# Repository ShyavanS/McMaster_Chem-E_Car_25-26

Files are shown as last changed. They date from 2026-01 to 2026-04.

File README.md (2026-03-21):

# McMaster_Chem-E_Car_25-26
The codebase for the McMaster Chem-E Car Team from 2025-2026.

This project uses an Adafruit Feather RP2040 Adalogger microcontroller programmed in the Arduino programming language. The car runs off a chemical reaction and is stopped by a chemical reaction as well. However, the code and the microcontroller are used to start the stopping reaction and stir the mixtures while monitoring it to identify when to stop based on a temperature threshold. It also uses an IMU to keep the car going straight, a servo for starting the stopping reaction, a switching circuit composed of solid-state relays to run the drive motors, and a motor driver for two auxiliary motors for stirring the braking reaction and operating accessories. The car's main drive system will be powered from a hydrogen fuel cell while the remaining auxiliary systems are powered from a smaller Li-Po battery.

The major components used are as follows:<br />
1 - N20 100 RPM Motor (for drive system)<br />
1 - N20 1000 RPM Motor (for reaction stirring mechanism)<br />
1 - N20 30 RPM Motor (for door actuation mechanism)<br />
3 - SER0039 Servo Motor (for initially mixing reactants & steering)<br />
1 - DRV8847 Motor Driver (for auxiliary motors)<br />
1 - AMT103 Rotary Encoder (for datalogging to tune braking model only)<br />
1 - CS326 Solid State Relay (for drive motors)<br />
1 - AD623 Instrumentation Amplifier (for braking reaction sensing setup)<br />
1 - GL5516 Phootoresistor (for braking reaction sensing setup)<br />
1 - 5 mm White LED (for braking reaction sensing setup)<br />
1 - REF2033 Dual-Output Voltage Reference (for braking reaction sensing setup)<br />
1 - INA219 Bidirectional Current/Power Monitor (for propulsion reaction datalogging & safety)<br />
1 - WS2812B LED Strip (for auxiliary lighting)<br />
1 - 2.5W Speaker (for auxiliary use)<br />
1 - PAM8302A Class D Amplifier (for driving speaker)<br />
1 - Toggle Switch (for enable line)<br />
1 - Adafruit 9-DOF Orientation IMU Fusion Breakout (BNO085 for logging/maintaining heading)<br /> 
1 - Adafruit Feather RP2040 Adalogger Microcontroller (for controlling the car)<br />
1 - 30W Hydrogen Fuel Cell  (for drive power)<br />
1 - 5000 mAh Li-Po Battery (for auxiliary power)<br />

This repository also contains the custom-made PCB design for the component wiring we are using this year. The design was made using Altium, source files & gerber files are present in this repository.

The main objective of the competition is to design a small car to carry a certain amount of weight a set distance while powering and stopping the vehicle with a chemical reaction. The distance and weight vary each year. The compectition is hosted by the American Institute of Chemical Engineers (AIChE).

Makes use of [pimoroni's encoder-pio driver](https://github.com/pimoroni/pimoroni-pico/tree/encoder-pio/drivers/encoder-pio) to count encoder ticks on the PIOs of the RP2040 to prefvent lost ticks due to higher priority interrupts and increase accuracy while decreasing CPU load. Minor modifications were made to remove debouncing functionality & delays.

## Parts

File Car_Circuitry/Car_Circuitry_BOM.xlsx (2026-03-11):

Comment | Description | Designator | Footprint | LibRef | Quantity
REF2033QDDCRQ1 | Integrated Circuit | AREF | SOT95P280X110-5N | REF2033QDDCRQ1 | 1
B2B-XH-A(LF)(SN) | CONN HEADER VERT 2POS 2.5MM | AUXM, DRVM, LEDB, PROP, SPKR, STRM, SW, TRB | FP-B2B-XH-A_LF_SN-MFG | CMP-2000-05888-3 | 8
TPS61023DRLT | Integrated Circuit | BOOST | SOTFL50P160X60-6N | TPS61023DRLT | 1
100 nF | Capacitor | C1, C4, C5, C8, C9, C13 | CAPC2012X95N | CL21B104KBCNNNC | 6
10 μF | Capacitor | C2, C6, C14 | CAPC2012X140N | CL21B106KOQNNNE | 3
1 μF | Capacitor | C3 | C0402C104J4RACTU | C0402C105K9PACTU | 1
10 μF | Capacitor Polarised | C7 | CAPPM3528X210N | 293D106X9016B2TE3 | 1
100 μF | Capacitor | C10 | GRM31x | GRM31CD80J107MEA8K | 1
220 pF | Capacitor | C11, C12 | GRM033D70J224ME01D | GRM033R71C221KA01D | 2
22 μF | Capacitor | C15, C16 | CAPC3216X180N | CL31B226KPHNNNE | 2
SMBJ18CA | TVS Diode (Bi-directional) | D1 | DIOM5436X261N | SMBJ18CA | 1
PAM8302AASCR | Integrated Circuit | DAMP | SOP65P490X110-8N | PAM8302AASCR | 1
DRV8847PWPR | Integrated Circuit | DRV | SOP65P640X120-17N | DRV8847PWPR | 1
61300411821 | THT Vertical Socket Header WR-PHD, Pitch 2.54 mm, Single Row, 4 pins | ENC | 61300411821 | CMP-1502-01316-4 | 1
MPZ1608S221ATA00 | Power line Ferrite Bead 220Ω @ 100MHz 2.2A DCR 0.05Ω SMD 0603 | FB1, FB2 | FP-MPZ1608-0_8-MFG | CMP-08257-000028-1 | 2
AD623ARZ-R7 | Integrated Circuit | IAMP | SOIC127P600X175-8N | AD623AR-REEL7 | 1
1 μH | Inductor | L1 | 74438357010 | 74438357010 | 1
B3B-XH-A(LF)(SN) | CONN HEADER VERT 3POS 2.5MM | LEDA, SVOB, SVOP, SVOS | FP-B3B-XH-A_LF_SN-MFG | CMP-17439-000014-3 | 4
Feather RP2040 Adalogger | Adafruit Microcontroller | MCU | 2796 | 2796 | 1
100 mΩ | Resistor | R1 | RESC2013X65N | RCWE0805R100FKEA | 1
400 Ω | Resistor | R2, R3 | RESC1608X46N | PAT0603E4000BST1 | 2
680 mΩ | Resistor | R4, R5 | ERJ6_B_BW_R_LW_CW_D | ERJ-6DQJR68V | 2
10 kΩ | Resistor | R6, R7 | RESC1005X40N | RC0402JR-0710KL | 2
200 kΩ | Resistor | R8 | ERA6AEB101V | ERA-6AEB204V | 1
330 Ω | Resistor | R9 | RESC1005X40N | RC0402FR-07330RL | 1
5 kΩ | Resistor | R10, R11, R13 | RESC0603X26N | TNPW02015K00BEED | 3
150 Ω | Resistor | R12 | RESC2012X60N | RK73B2ATTD151J | 1
100 kΩ | Resistor | R14 | ERJ8ENF1000V | ERJ-8ENF1003V | 1
732 kΩ | Resistor | R15 | ERJ8ENF1000V | ERJ-8ENF7323V | 1
CS326 | Relay or Contactor | SSR | SOP254P1030X390-8N | CS326 | 1
INA219BIDR | Integrated Circuit | VAM | SOIC127P600X175-8N | INA219BIDR | 1

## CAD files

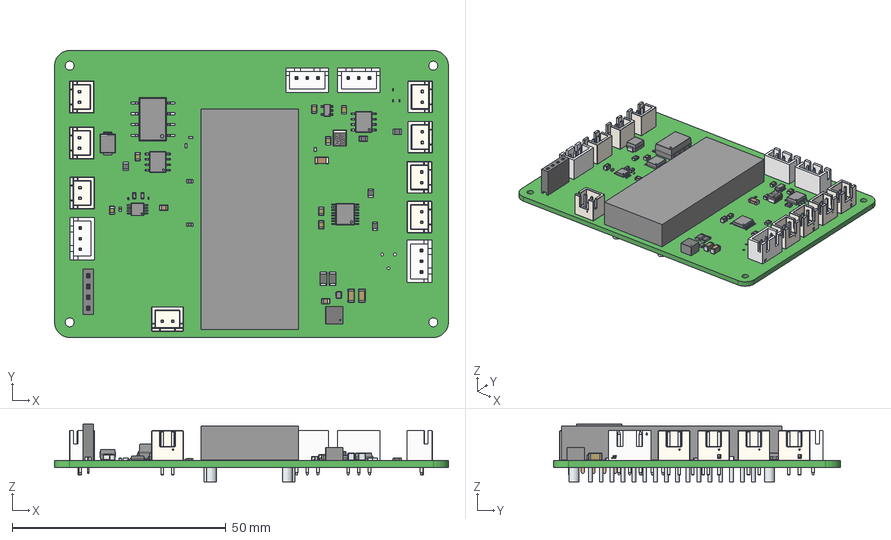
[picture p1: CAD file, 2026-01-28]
Car_Circuitry/Car_Circuitry.step
92.1 x 67.1 x 13.5 mm
PinsArrayLR x 5
term1 x 4
term2 x 4
B2B-XH-A x 8
JST Logo adjustable x 8
solidBody x 5
solidTop x 5
solidTerminal1
solidTerminal2
solidTerminal3
GCM31A5C2J820JX01J_3
GCM31A5C2J820JX01J_2
GCM31A5C2J820JX01J
PinsArrayL
PinsArrayR
terminals x 2
logo x 2
Pins x 4
Marking x 4
JST Logo x 4
6130xx11821_PIN x 4
body_SSMC_4030
land_pattern_SSMC_4020 x 2
Terminal x 4
Leads x 32
ThermalPad
BODY-SOT
PIN1-ID

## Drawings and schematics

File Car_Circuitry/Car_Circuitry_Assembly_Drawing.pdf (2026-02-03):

13

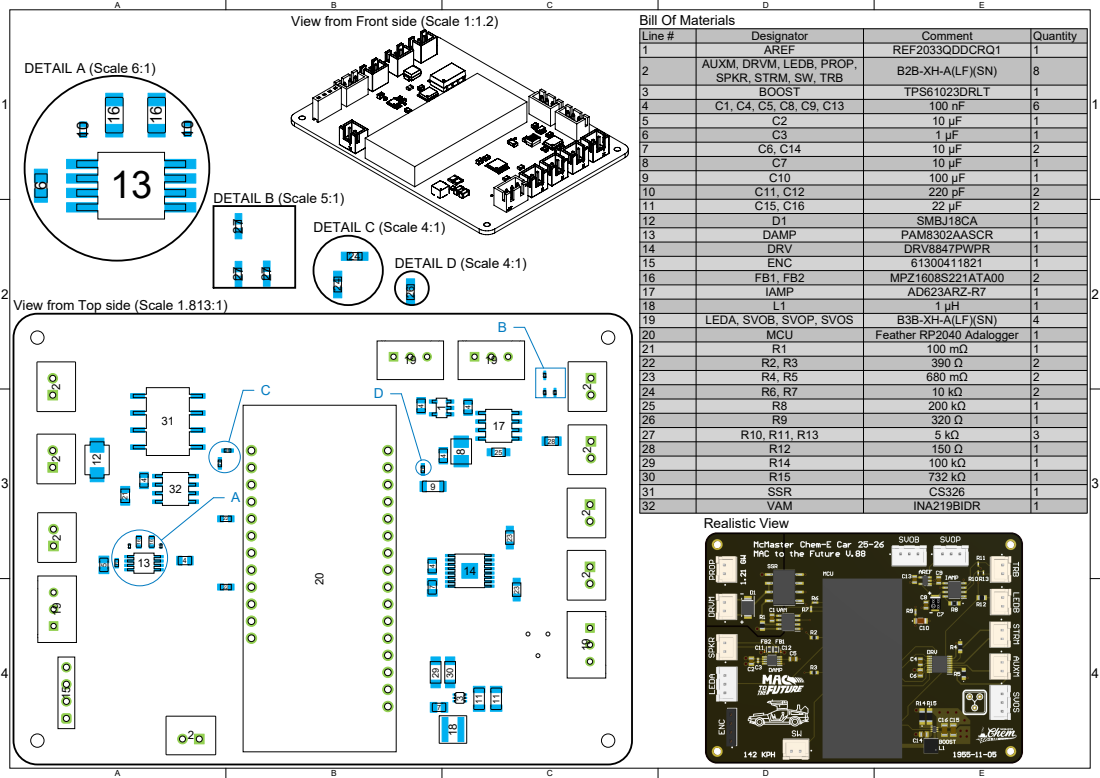
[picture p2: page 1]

View from Front side (Scale 1:1.2)

Line # | Designator | Comment | Quantity
1 | AREF | REF2033QDDCRQ1 | 1
2 | AUXM, DRVM, LEDB, PROP, SPKR, STRM, SW, TRB | B2B-XH-A(LF)(SN) | 8

3 | BOOST | TPS61023DRLT | 1
4 | C1, C4, C5, C8, C9, C13 | 100 nF | 6
5 | C2 | 10 μF | 1
6 | C3 | 1 μF | 1
7 | C6, C14 | 10 μF | 2
8 | C7 | 10 μF | 1
9 | C10 | 100 μF | 1
10 | C11, C12 | 220 pF | 2
11 | C15, C16 | 22 μF | 2
12 | D1 | SMBJ18CA | 1
13 | DAMP | PAM8302AASCR | 1
14 | DRV | DRV8847PWPR | 1
15 | ENC | 61300411821 | 1
16 | FB1, FB2 | MPZ1608S221ATA00 | 2
17 | IAMP | AD623ARZ-R7 | 1
18 | L1 | 1 μH | 1
19 | LEDA, SVOB, SVOP, SVOS | B3B-XH-A(LF)(SN) | 4
20 | MCU | Feather RP2040 Adalogger | 1
21 | R1 | 100 mΩ | 1
22 | R2, R3 | 390 Ω | 2
23 | R4, R5 | 680 mΩ | 2
24 | R6, R7 | 10 kΩ | 2
25 | R8 | 200 kΩ | 1
26 | R9 | 320 Ω | 1
27 | R10, R11, R13 | 5 kΩ | 3
28 | R12 | 150 Ω | 1

View from Top side (Scale 1.813:1)

29 | R14 | 100 kΩ | 1
30 | R15 | 732 kΩ | 1
31 | SSR | CS326 | 1
32 | VAM | INA219BIDR | 1

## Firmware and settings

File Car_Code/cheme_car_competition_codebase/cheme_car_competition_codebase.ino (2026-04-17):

// McMaster Chem-E Car Team
// Chem-E Car Competition Code - 25/26

/*
The code to be used at the Chem-E Car competition to run the car. Makes use of
an RP2040 microcontroller to drive the car and stop at a specified distance.
More information is available in the readme.
*/

// Included libraries
#include <Adafruit_BNO08x.h>
#include <Servo.h>
#include <Adafruit_NeoPixel.h>
#include <Wire.h>
#include <BackgroundAudio.h>
#include <PWMAudio.h>
#include <SdFat.h>
#include "hardware/timer.h"
#include "pico/stdlib.h"

#define NUM_LEDS 1    // Status LED
#define STRIP_LEDS 22 // LED Strip

// Define drive and brake SSR pins
#define DRIVE_PIN 9
#define BRAKE_PIN 13

// Define the PWM pins for the stir bar motors
#define BRAK_STIR_PWM_1 A3
#define BRAK_STIR_PWM_2 24

// Define servo pins
#define BRAK_SERVO_PWM 11
#define PROP_SERVO_PWM 4
#define STEERING_SERVO_PWM 25

// Define Auxillary DC Motor Pins
#define AUXDC_PWM_1 6
#define AUXDC_PWM_2 5

#define STRIP_PIN 10 // Light pin

#define TURBIDITY_SENS A2 // Pin for the turbidity sensor data line(right encoder and braking sensor switched pins)
#define BNO08X_RESET -1   // No reset pin for IMU over I2C, only enabled for SPI
#define SD_CS_PIN 23      // Define chip select pin for SD card
#define A219_I2C 0x40     // I2C address for current/voltage sensor
#define AUDIO_OUT 12      // Define audio output pin

// Struct for Euler Angles
struct euler_t
{
  float yaw;
  float pitch;
  float roll;
} ypr;

// Enumeration for door commands
enum door_cmd
{
  DOOR_STOP,
  DOOR_OPEN,
  DOOR_CLOSE
};

// Enumeration for multicore commands
enum mutlicore_cmd
{
  PLAY_DOOR_OPEN = 1,
  PLAY_DOOR_CLOSE,
  PLAY_TIME_TRAVEL,
  PLAY_TIME_CIRCUIT,
  STATUS_ERROR,
  STATUS_STARTED,
  STATUS_STOPPED,
  SD_INITIALIZED
};

// Create servo objects
Servo brak_servo;
Servo prop_servo;
Servo steering_servo;

// Create BNO085 instance
Adafruit_BNO08x bno08x(BNO08X_RESET);
sh2_SensorValue_t sensor_value;

Adafruit_NeoPixel pixel(NUM_LEDS, PIN_NEOPIXEL, NEO_GRB + NEO_KHZ800); // Status LED
Adafruit_NeoPixel strip(STRIP_LEDS, STRIP_PIN, NEO_GRB + NEO_KHZ800);  // Strip LEDs

// Define files
SdFat sd;
FsFile audio_file;
String door_close_sound = "door_close_sound.mp3";
String time_circuit_sound = "time_circuit_sound.mp3";
String time_travel_sound = "time_travel_sound.mp3";
String door_open_sound = "door_open_sound.mp3";
String theme_music = "theme_music.mp3";
SdSpiConfig config(SD_CS_PIN, DEDICATED_SPI, SD_SCK_MHZ(16), &SPI1);
String file_name;

// Set up audio output using PWM
PWMAudio pwm(AUDIO_OUT);
BackgroundAudioMP3 mp3(pwm); // create the mp3 player object and decoder
uint8_t filebuff[512];       // allocates 512 bytes of memory to temporarily store audio data before processing

// LED variables
bool breath_status = false;
bool fluxing = false;
bool time_jump = false;
int breath_brightness = 0;
int t = 0;
uint32_t tic;
uint32_t toc;

bool sd_init = false; // SD intialization flag

// Runtime flags
volatile bool running = true;
volatile bool audio_trig = false;
volatile unsigned int audio_played = 0;

// The target yaw angle to keep car straight
const float GOAL_YAW = 0.0;

// Rejection threshold for noise in IMU measurements
const float REJECT_THRESHOLD = 3.0;

// define turbidity threshold for braking
const float TURB_THRESHOLD = 3500.0;

// Define voltage & current monitor variables
uint16_t raw_bus;
int16_t raw_current;
double bus_voltage;
double current_mA;

// Define IMU variables
double raw_yaw;        // raw yaw angle
double prev_yaw;       // previous unwrapped yaw angle
double yaw;            // unwrapped yaw angle
double init_yaw = 0.0; // initial yaw angle
double yaw_diff = 0.0; // yaw angle difference

double turbidity; // turbidity counts

// Keeping track of time
double curr_time = 0.0f;
double prev_time = 0.0f;
uint32_t start_time;

// PID loop variables
double error = 0.0;      // Proportional error
double last_error = 0.0; // Derivative error
double sum_error = 0.0;  // Integral error

// Current values obtained through Ziegler–Nichols method with K_u = 30 & T_u = 266.7 ms.
// Divide derivative term by 100 to make sense on this timescale
// Added 4 to proportional since speed was changed with higher gearing
const float K_P = 22.0;  // Proportional weighting
const float K_I = 0.135; // Integral weighting
const float K_D = 0.612; // Derivative weighting

// Offsets & constants for PID
const int SERVO_ANGLE = 1475;
const int MAX_OFFSET = 1024;
const int YAW_REF = 90;

/*
Description: Subroutine to close both drive and brake SSR.
Inputs:      void
Outputs:     void
Parameters:  void
Returns:     void
*/
void reset_ssr()
{
  digitalWrite(DRIVE_PIN, LOW);
  digitalWrite(BRAKE_PIN, LOW);
}

/*
Description: Subroutine to drive car forward.
Inputs:      void
Outputs:     void
Parameters:  void
Returns:     void
*/
void drive_ssr()
{
  reset_ssr();
  busy_wait_ms(1);
  digitalWrite(DRIVE_PIN, HIGH);
}

/*
Description: Subroutine to stop car and brake motors.
Inputs:      void
Outputs:     void
Parameters:  void
Returns:     void
*/
void brake_ssr()
{
  reset_ssr();
  busy_wait_ms(1);
  digitalWrite(BRAKE_PIN, HIGH);
}

/*
Description: Subroutine to dump reactants into vessel.
Inputs:      void
Outputs:     void
Parameters:  (Servo)servo, (int)angle_us, (int)delay_ms
Returns:     void
*/
void servo_dump(Servo servo, int angle_us, int delay_ms)
{
  // Rotate to specified position
  servo.writeMicroseconds(angle_us);
  busy_wait_ms(500);
  servo.writeMicroseconds(angle_us);

  busy_wait_ms(delay_ms); // Wait specified delay

  // Return to default position
  servo.writeMicroseconds(450);
  busy_wait_ms(500);
  servo.writeMicroseconds(450);
}

/*
Description: Subroutine to set speed for reaction stir motors.
Inputs:      void
Outputs:     void
Parameters:  (int)stir_pin_1, (int)stir_pin_2, (int)speed
Returns:     void
*/
void start_stir(int stir_pin_1, int stir_pin_2, int speed)
{
  digitalWrite(stir_pin_1, LOW); // For fast decay
  analogWrite(stir_pin_2, 255);  // Set motor to max for a kickstart
  busy_wait_ms(1000);
  digitalWrite(stir_pin_1, LOW);  // For fast decay
  analogWrite(stir_pin_2, speed); // Set motor to speed obtained through testing
}

/*
Description: Subroutine to stop reaction stir motors.
Inputs:      void
Outputs:     void
Parameters:  (int)stir_pin_1, (int)stir_pin_2
Returns:     void
*/
void stop_stir(int stir_pin_1, int stir_pin_2)
{
  digitalWrite(stir_pin_1, LOW); // For fast decay
  digitalWrite(stir_pin_2, LOW); // Stop motor
}

/*
Description: Subroutine to command the door motor
Inputs:      void
Outputs:     void
Parameters:  (door_cmd)cmd, (int)speed
Returns:     void
*/
void door_motor(door_cmd cmd, int speed)
{
  switch (cmd)
  {
  case DOOR_STOP:
    analogWrite(AUXDC_PWM_1, 0);
    analogWrite(AUXDC_PWM_2, 0);
    break;
  case DOOR_OPEN:
    analogWrite(AUXDC_PWM_1, 0);
    analogWrite(AUXDC_PWM_2, speed);
    break;
  case DOOR_CLOSE:
    analogWrite(AUXDC_PWM_1, speed);
    analogWrite(AUXDC_PWM_2, 0);
    break;
  default:
    break;
  }
}

/*
Description: Subroutine to set the desired reports on the IMU.
Inputs:      void
Outputs:     void
Parameters:  void
Returns:     void
*/
void set_reports(void)
{
  if (!bno08x.enableReport(SH2_ROTATION_VECTOR))
  {
    exit(0);
  }
}

/*
Description: Subroutine convert quaternions from the IMU into euler angles to obtain yaw.
Inputs:      void
Outputs:     void
Parameters:  (float)qr, (float)qi, (float)qj, (float)qk, (euler_t)*ypr, (bool)degrees
Returns:     void
*/
void quaternion_to_euler(float qr, float qi, float qj, float qk, euler_t *ypr, bool degrees = false)
{
  float sqr = sq(qr);
  float sqi = sq(qi);
  float sqj = sq(qj);
  float sqk = sq(qk);

  ypr->yaw = atan2(2.0 * (qi * qj + qk * qr), (sqi - sqj - sqk + sqr));
  ypr->pitch = asin(-2.0 * (qi * qk - qj * qr) / (sqi + sqj + sqk + sqr));
  ypr->roll = atan2(2.0 * (qj * qk + qi * qr), (-sqi - sqj + sqk + sqr));

  if (degrees)
  {
    ypr->yaw *= RAD_TO_DEG;
    ypr->pitch *= RAD_TO_DEG;
    ypr->roll *= RAD_TO_DEG;
  }
}

/*
Description: Pointer subroutine for euler angles.
Inputs:      void
Outputs:     void
Parameters:  (sh2_RotationVectorWAcc_t)*rotational_vector, (float)qi, (euler_t)*ypr, (bool)degrees
Returns:     void
*/
void quaternion_to_euler_RV(sh2_RotationVectorWAcc_t *rotational_vector, euler_t *ypr, bool degrees = false)
{
  quaternion_to_euler(rotational_vector->real, rotational_vector->i, rotational_vector->j, rotational_vector->k, ypr, degrees);
}

/*
Description: PID loop subroutine to adjust steering angle.
Inputs:      (double)error, (double)sum_error, (double)last_error, (double)curr_time, (double)prev_time
Outputs:     (int)adj_pid_output
Parameters:  void
Returns:     void
*/
void pid_loop(void)
{
  // Generate output of controller based on constants & errors
  double pid_output = (error * K_P + sum_error * K_I + (error - last_error) / (curr_time - prev_time) * K_D) / YAW_REF * MAX_OFFSET;
  int adj_pid_output = max(min(round(pid_output), MAX_OFFSET), -MAX_OFFSET); // Clamp output to bounds

  // Get IMU reading to update error values
  bno08x.getSensorEvent(&sensor_value);
  quaternion_to_euler_RV(&sensor_value.un.rotationVector, &ypr, true);

  // Process yaw angle
  raw_yaw = ypr.yaw;
  unwrap_yaw();
  yaw_diff = yaw - init_yaw;

  // Update errors
  last_error = error;
  error = GOAL_YAW - yaw_diff;
  sum_error = max(min(sum_error + error, MAX_OFFSET), -MAX_OFFSET);

  // Write to servos
  steering_servo.writeMicroseconds(SERVO_ANGLE + adj_pid_output);
}

/*
Description: Subroutine to fetch turbidity samples and output the average value.
Inputs:      void
Outputs:     void
Parameters:  (int)samples
Returns:     (float)turbidity
*/
float fetch_turb(int samples)
{
  // calculate turbidity (avg of # measurements)
  float turbidity = 0.0f;

  for (int i = 0; i < samples; i++)
  {
    turbidity += (double)analogRead(TURBIDITY_SENS);
  }
  turbidity = turbidity / (double)samples;

  return turbidity;
}

/*
Description: Subroutine to unwrap yaw angle to prevent discontinuities in the function over time.
Inputs:      (double)raw_yaw, (double)prev_yaw
Outputs:     (double)yaw
Parameters:  void
Returns:     void
*/
void unwrap_yaw(void)
{
  double delta = raw_yaw - prev_yaw;

  delta = fmod(delta + 180.0, 360.0);

  if (delta < 0.0)
  {
    delta += 360.0;
  }

  delta -= 180.0;

  // Reject any sudden noisy spikes
  if (fabs(delta) > REJECT_THRESHOLD)
  {
    yaw = prev_yaw;
    prev_yaw = yaw;
  }
  else
  {
    yaw = prev_yaw + delta;
    prev_yaw = yaw;
  }
}

/*
Description: Turn on speaker before playing audio
Inputs:      void
Outputs:     void
Parameters:  void
Returns:     void
*/
void stop_speaker(void)
{
  while (!audio_file && !mp3.done())
    ;

  memset(filebuff, 0, 512);
  mp3.write(filebuff, 512);
}
/*
Description: Send audio data chunks to the decoder and close file when done
Inputs:      void
Outputs:     void
Parameters:  void
Returns:     void
*/
void send_audio(void)
{
  // If an audio file is open and the decoder buffer has enough space for more audio data
  if (audio_file && mp3.availableForWrite() > 512)
  {
    // read 512 bytes from the audio file and send to the decoder
    int len = audio_file.read(filebuff, 512);
    mp3.write(filebuff, len);

    // if the audio data was shorter than 512 bytes, we've reached the end of the file
    if (len != 512)
    {
      audio_trig = false;
      audio_played++;

      audio_file.close();
      stop_speaker();
    }
  }
}

/*
Description: Activates Orange/Blue car lights
Inputs: void
Outputs: void
Parameters: void
Returns: void
*/
void car_lights(void)
{
  if (!breath_status)
  {
    breath_brightness += 10;

    if (breath_brightness >= 255)
    {
      breath_brightness = 255;
      breath_status = true;
    }

    for (int i = 1; i < STRIP_LEDS; i++)
    {
      strip.setPixelColor(i, 0, (int)255 * breath_brightness / 255, (int)255 * breath_brightness / 255); // set rest of pixels blue for now...
    }
  }
  else
  {
    int spark = random(0, 50);

    if (spark < 5)
    {
      for (int i = 1; i < STRIP_LEDS; i++)
      {
        strip.setPixelColor(i, 255, 40, 0); // set rest of pixels orange for now...
      }
    }
    else
    {
      for (int i = 1; i < STRIP_LEDS; i++)
      {
        strip.setPixelColor(i, 0, 255, 255); // set rest of pixels blue for now...
      }
    }
  }

  strip.setPixelColor(0, 255, 255, 255);
  strip.show();
}

/*
Description: Turns on flux capacitor light
Inputs: void
Outputs: void
Parameters: void
Returns: void
*/
void flux_cap(void)
{
  t++;

  // Base sinusoid + flicker
  float wave = (sin(t * 0.1) + 1) * 0.5;
  int base = 120 + wave * 100;
  int flicker = random(-40, 40);
  int b = constrain(base + flicker, 0, 255);

  // Sudden burst for extra random behaviour
  int burst = random(0, 50);

  if (burst < 10)
  {
    b = 255;
  }
  else if (burst > 40)
  {
    b = 0;
  }

  strip.setPixelColor(0, b, b, b);
  strip.show();
}

/*
Description: Helper function to write value to register over I2C
Inputs: void
Outputs: void
Parameters: (uint8_t)address, (uint8_t)reg, (uint16_t)value
Returns: void
*/
void write_register(uint8_t address, uint8_t reg, uint16_t value)
{
  Wire.beginTransmission(address);

  Wire.write(reg);
  Wire.write((value >> 8) & 0xFF); // MSB
  Wire.write(value & 0xFF);        // LSB

  Wire.endTransmission();
}

/*
Description: Helper function to read value from register over I2C
Inputs: void
Outputs: void
Parameters: (uint8_t)address, (uint8_t)reg
Returns: (uint16_t)value
*/
uint16_t read_register(uint8_t address, uint8_t reg)
{
  Wire.beginTransmission(address);
  Wire.write(reg);
  Wire.endTransmission();

  Wire.requestFrom(address, (uint8_t)2); // Request 2 bytes

  // If data available then return it
  if (Wire.available() >= 2)
  {
    uint16_t value = Wire.read() << 8;
    value |= Wire.read();
    return value;
  }

  return 0; // Otherwise return 0
}

/*
Description: Arduino core 0 setup subroutine.
Inputs:      void
Outputs:     void
Parameters:  void
Returns:     void
*/
void setup(void)
{
  // Intitalize Voltage/Current Sensor
  Wire.begin();

  // Write to config register (0x00), Sets it to 16V bus range, Gain /4, 12 bit ADC, Continuous Mode, 8-sample averaging
  write_register(A219_I2C, 0x00, 0x15DF);

  // Write to calibration register (0x05), 0.1 Ohm resistor and 2.0A max current (0.1 mA per bit)
  // Uses formula 0.04096/(Resistor*Current_Per_Bit), 12 bit scaling
  write_register(A219_I2C, 0x05, 0x1000);

  // --- READ BUS VOLTAGE (0x02) ---
  raw_bus = read_register(A219_I2C, 0x02);
  // Shift right 3 bits to remove status flags, then multiply by 4mV
  bus_voltage = (raw_bus >> 3) * 0.004;

  // --- READ CURRENT (0x04) ---
  raw_current = (int16_t)read_register(A219_I2C, 0x04);
  // Multiply by calculated LSB (0.1mA)
  current_mA = raw_current * 0.1;

  // Block if SD not initialized for 3 seconds, then move on
  uint32_t cmd = 0;
  start_time = time_us_32();

  while (!rp2040.fifo.pop_nb(&cmd) && time_us_32() - start_time < 3000000)
    ;

  if (cmd == SD_INITIALIZED)
  {
    sd_init = true;
  }

  // Setting to drive,brake motors output mode
  pinMode(DRIVE_PIN, OUTPUT);
  pinMode(BRAKE_PIN, OUTPUT);

  brake_ssr(); // Stop driving motors from any residual bootloader code

  // Initialize the auxiliary DC motor pins as outputs
  pinMode(BRAK_STIR_PWM_1, OUTPUT);
  pinMode(BRAK_STIR_PWM_2, OUTPUT);
  pinMode(AUXDC_PWM_1, OUTPUT);
  pinMode(AUXDC_PWM_2, OUTPUT);

  // Setting the stir speed
  start_stir(BRAK_STIR_PWM_1, BRAK_STIR_PWM_2, 154);

  analogReadResolution(12);
  pinMode(TURBIDITY_SENS, INPUT);
  bno08x.begin_I2C();
  set_reports();

  // Poll IMU a few times & wait for initialization value to stabilize
  for (int i = 0; i < 5; i++)
  {
    bno08x.getSensorEvent(&sensor_value);
    quaternion_to_euler_RV(&sensor_value.un.rotationVector, &ypr, true);

    init_yaw = ypr.yaw;
    raw_yaw = init_yaw;
    prev_yaw = init_yaw;
    yaw = init_yaw;
    yaw_diff = yaw - init_yaw;

    busy_wait_ms(200);
  }

  door_motor(DOOR_CLOSE, 154); // Start closing door

  rp2040.fifo.push(PLAY_DOOR_CLOSE);

  while (audio_played == 0 && sd_init)
    ;

  door_motor(DOOR_STOP, 0); // Stop closing door

  // Initialize servos to default position
  prop_servo.writeMicroseconds(450);
  prop_servo.attach(PROP_SERVO_PWM, 400, 2600);
  prop_servo.writeMicroseconds(450);
  brak_servo.writeMicroseconds(450);
  brak_servo.attach(BRAK_SERVO_PWM, 400, 2600);
  brak_servo.writeMicroseconds(450);
  steering_servo.writeMicroseconds(1475);
  steering_servo.attach(STEERING_SERVO_PWM, 400, 2600);
  steering_servo.writeMicroseconds(1475);

  // Dump reactants before starting drive
  servo_dump(prop_servo, 2500, 1000);

  // Wait for busVolatge to surpass 9V
  while (bus_voltage < 9)
  {
    raw_bus = read_register(A219_I2C, 0x02);
    bus_voltage = (raw_bus >> 3) * 0.004;
  }

  rp2040.fifo.push(PLAY_TIME_CIRCUIT);

  while (audio_played == 1 && sd_init)
    ;

  servo_dump(brak_servo, 2500, 3000);

  start_time = time_us_32(); // Braking start time

  // Poll IMU one last time
  bno08x.getSensorEvent(&sensor_value);
  quaternion_to_euler_RV(&sensor_value.un.rotationVector, &ypr, true);

  init_yaw = ypr.yaw;
  raw_yaw = init_yaw;
  prev_yaw = init_yaw;
  yaw = init_yaw;
  yaw_diff = yaw - init_yaw;

  curr_time = (time_us_32() - start_time) / 1000000.0f; // Taken to update prev_time

  rp2040.fifo.push(STATUS_STARTED);

  drive_ssr(); // Start drive
}

/*
Description: Arduino core 0 loop subroutine.
Inputs:      void
Outputs:     void
Parameters:  void
Returns:     void
*/
void loop(void)
{
  prev_time = curr_time;

  turbidity = fetch_turb(20); // fetch turbidity measurement

  curr_time = (time_us_32() - start_time) / 1000000.0f; // Taken to check time against first measurement

  if (running)
  {
    pid_loop(); // Run PID controller
  }

  raw_bus = read_register(A219_I2C, 0x02);
  bus_voltage = (raw_bus >> 3) * 0.004;

  raw_current = (int16_t)read_register(A219_I2C, 0x04);
  current_mA = raw_current * 0.1;

  // If outside of 7-13V range of > 1A current draw then stop
  if (bus_voltage > 13 || bus_voltage < 7 || current_mA > 1000)
  {
    brake_ssr();
    rp2040.fifo.push(STATUS_ERROR);
  }

  if (turbidity >= TURB_THRESHOLD && running)
  {
    brake_ssr();                                 // Stop driving
    stop_stir(BRAK_STIR_PWM_1, BRAK_STIR_PWM_2); // Stop stirring motor

    rp2040.fifo.push(STATUS_STOPPED);

    running = false; // Set flag
  }

  if (!running)
  {
    if (audio_played == 2 && !audio_trig) // Play sound effect for time travel
    {
      rp2040.fifo.push(PLAY_TIME_TRAVEL);
      audio_trig = true;
    }
    else if (audio_played == 3 && !audio_trig) // Play sound effect for doors
    {
      busy_wait_ms(500);
      door_motor(DOOR_OPEN, 255); // Start opening door
      rp2040.fifo.push(PLAY_DOOR_OPEN);

      audio_trig = true;
    }
    else if (audio_played == 4 && !audio_trig) // Done everything, run once
    {
      door_motor(DOOR_STOP, 0); // Stop opening door
      audio_trig = true;
    }
  }
}

/*
Description: Arduino core 1 setup subroutine.
Inputs:      void
Outputs:     void
Parameters:  void
Returns:     void
*/
void setup1(void)
{
  mp3.begin();    // Start speaker
  stop_speaker(); // Don't overheat speaker

  // Indicate status to be initialized
  pixel.begin();
  pixel.setBrightness(255);
  pixel.setPixelColor(0, 255, 0, 0);
  pixel.show();

  // LED strips
  strip.begin();
  strip.setBrightness(255);

  for (int i = 0; i < STRIP_LEDS; i++)
  {
    strip.setPixelColor(i, 0, 0, 0);
  }

  strip.show();

  mp3.begin(); // Initialize mp3 module

  bool configured = sd.begin(config); // Initialize the SD card without blocking in case it doesn't read

  if (configured)
  {
    rp2040.fifo.push(SD_INITIALIZED);
  }

  toc = time_us_32(); // Set last update variable
}

/*
Description: Arduino core 1 loop subroutine.
Inputs:      void
Outputs:     void
Parameters:  void
Returns:     void
*/
void loop1(void)
{
  uint32_t cmd = 0;
  tic = time_us_32();

  rp2040.fifo.pop_nb(&cmd);

  switch (cmd)
  {
  case PLAY_DOOR_OPEN:
    audio_file = sd.open(door_open_sound, FILE_READ); // Open corresponding SD card mp3 file
    break;
  case PLAY_DOOR_CLOSE:
    audio_file = sd.open(door_close_sound, FILE_READ); // Open corresponding SD card mp3 file
    break;
  case PLAY_TIME_TRAVEL:
    fluxing = false;
    time_jump = true;
    audio_file = sd.open(time_travel_sound, FILE_READ); // Open corresponding SD card mp3 file
    break;
  case PLAY_TIME_CIRCUIT:
    fluxing = true;
    audio_file = sd.open(time_circuit_sound, FILE_READ); // Open corresponding SD card mp3 file
    break;
  case STATUS_ERROR:
    pixel.setPixelColor(0, 255, 0, 0); // Indicate error status
    pixel.show();
    break;
  case STATUS_STARTED:
    audio_file = sd.open(theme_music, FILE_READ); // Open corresponding SD card mp3 file
    pixel.setPixelColor(0, 0, 0, 255);            // Indicate setup complete status
    pixel.show();
    break;
  case STATUS_STOPPED:
    audio_file.close();
    stop_speaker();
    pixel.setPixelColor(0, 0, 255, 0); // Indicate status to be finished
    pixel.show();
    break;
  default:
    break;
  }

  if (audio_file) // If the audio file opened successfully
  {
    send_audio(); // If the audio file has been opened and is still open, send an audio data chunk
  }

  if (fluxing)
  {
    flux_cap();
  }

  if (audio_played == 2 && !running && tic - toc > 25000)
  {
    toc = time_us_32();
    car_lights();
  }
  else if (!running && time_jump && audio_played != 2)
  {
    time_jump = false;

    for (int i = 0; i < STRIP_LEDS; i++)
    {
      strip.setPixelColor(i, 0, 0, 0);
    }

    strip.show();
  }
}

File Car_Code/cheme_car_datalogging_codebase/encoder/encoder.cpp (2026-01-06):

#include <math.h>
#include <float.h>
#include "hardware/irq.h"
#include "hardware/clocks.h"
#include "encoder.hpp"

#ifndef NO_QSTR
#include "encoder.pio.h"
#endif

#define LAST_STATE(state) ((state) & 0b0011)
#define CURR_STATE(state) (((state) & 0b1100) >> 2)

namespace encoder
{

  ////////////////////////////////////////////////////////////////////////////////////////////////////
  // STATICS
  ////////////////////////////////////////////////////////////////////////////////////////////////////
  Encoder *Encoder::encoders[][NUM_PIO_STATE_MACHINES] = {{nullptr, nullptr, nullptr, nullptr}, {nullptr, nullptr, nullptr, nullptr}};
  uint8_t Encoder::claimed_sms[] = {0x0, 0x0};
  uint Encoder::pio_program_offset[] = {0, 0};

  Encoder::Capture::Capture()
      : captured_count(0), captured_delta(0), captured_frequency(0.0f), counts_per_rev(INT32_MAX)
  {
  }

  Encoder::Capture::Capture(int32_t count, int32_t delta, float frequency, float counts_per_rev)
      : captured_count(count), captured_delta(delta), captured_frequency(frequency), counts_per_rev(MAX(counts_per_rev, FLT_EPSILON))
  { // Clamp counts_per_rev to avoid potential NaN
  }

  int32_t Encoder::Capture::count() const
  {
    return captured_count;
  }

  int32_t Encoder::Capture::delta() const
  {
    return captured_delta;
  }

  float Encoder::Capture::frequency() const
  {
    return captured_frequency;
  }

  float Encoder::Capture::revolutions() const
  {
    return (float)captured_count / counts_per_rev;
  }

  float Encoder::Capture::degrees() const
  {
    return revolutions() * 360.0f;
  }

  float Encoder::Capture::radians() const
  {
    return revolutions() * M_TWOPI;
  }

  float Encoder::Capture::revolutions_delta() const
  {
    return (float)captured_delta / counts_per_rev;
  }

  float Encoder::Capture::degrees_delta() const
  {
    return revolutions_delta() * 360.0f;
  }

  float Encoder::Capture::radians_delta() const
  {
    return revolutions_delta() * M_TWOPI;
  }

  float Encoder::Capture::revolutions_per_second() const
  {
    return captured_frequency / counts_per_rev;
  }

  float Encoder::Capture::revolutions_per_minute() const
  {
    return revolutions_per_second() * 60.0f;
  }

  float Encoder::Capture::degrees_per_second() const
  {
    return revolutions_per_second() * 360.0f;
  }

  float Encoder::Capture::radians_per_second() const
  {
    return revolutions_per_second() * M_TWOPI;
  }

  Encoder::Encoder(PIO pio, uint sm, const pin_pair &pins, uint common_pin, Direction direction,
                   float counts_per_rev, bool count_microsteps, uint16_t freq_divider)
      : pio(pio), sm(sm), enc_pins(pins), enc_common_pin(common_pin), enc_direction(direction), enc_counts_per_rev(MAX(counts_per_rev, FLT_EPSILON)), count_microsteps(count_microsteps), freq_divider(freq_divider), clocks_per_time((float)(clock_get_hz(clk_sys) / (ENC_LOOP_CYCLES * freq_divider)))
  {
  }

  Encoder::~Encoder()
  {
    if (initialised)
    {
      pio_sm_set_enabled(pio, sm, false);
      pio_sm_unclaim(pio, sm);

      uint pio_idx = pio_get_index(pio);
      encoders[pio_idx][sm] = nullptr;
      claimed_sms[pio_idx] &= ~(1u << sm);

      hw_clear_bits(&pio->inte1, PIO_IRQ1_INTE_SM0_RXNEMPTY_BITS << sm);

      // If there are no more SMs using the encoder program, then we can remove it from the PIO
      if (claimed_sms[pio_idx] == 0)
      {
        pio_remove_program(pio, &encoder_program, pio_program_offset[pio_idx]);

        if (pio_idx == 0)
        {
          irq_remove_handler(PIO0_IRQ_1, pio0_interrupt_handler);
        }
        else
        {
          irq_remove_handler(PIO1_IRQ_1, pio1_interrupt_handler);
        }
      }

      // Reset all the pins this PWM will control back to an unused state
      gpio_set_function(enc_pins.a, GPIO_FUNC_NULL);
      gpio_set_function(enc_pins.b, GPIO_FUNC_NULL);

      if (enc_common_pin != PIN_UNUSED)
      {
        gpio_set_function(enc_common_pin, GPIO_FUNC_NULL);
      }
    }
  }

  void Encoder::pio_interrupt_handler(uint pio_idx)
  {
    // Go through each SM on the PIO to see which triggered this interrupt,
    // and if there's an associated encoder, have it update its state
    for (uint8_t sm = 0; sm < NUM_PIO_STATE_MACHINES; sm++)
    {
      if (encoders[pio_idx][sm] != nullptr)
      {
        encoders[pio_idx][sm]->process_steps();
      }
    }
  }

  void Encoder::pio0_interrupt_handler()
  {
    pio_interrupt_handler(0);
  }

  void Encoder::pio1_interrupt_handler()
  {
    pio_interrupt_handler(1);
  }

  bool Encoder::init()
  {
    if (!initialised && !pio_sm_is_claimed(pio, sm))
    {
      // Are the pins we want to use actually valid?
      if ((enc_pins.a < NUM_BANK0_GPIOS) && (enc_pins.b < NUM_BANK0_GPIOS))
      {

        // If a Pin C was defined, and valid, set it as a GND to pull the other two pins down
        if ((enc_common_pin != PIN_UNUSED) && (enc_common_pin < NUM_BANK0_GPIOS))
        {
          gpio_init(enc_common_pin);
          gpio_set_dir(enc_common_pin, GPIO_OUT);
          gpio_put(enc_common_pin, false);
        }

        pio_sm_claim(pio, sm);
        uint pio_idx = pio_get_index(pio);

        // If this is the first time using an encoder on this PIO, add the program to the PIO memory
        if (claimed_sms[pio_idx] == 0)
        {
          pio_program_offset[pio_idx] = pio_add_program(pio, &encoder_program);
        }

        // Initialise the A and B pins of this encoder
        pio_gpio_init(pio, enc_pins.a);
        pio_gpio_init(pio, enc_pins.b);
        gpio_pull_up(enc_pins.a);
        gpio_pull_up(enc_pins.b);

        // Set their default direction
        pio_sm_set_consecutive_pindirs(pio, sm, enc_pins.a, 1, false);
        pio_sm_set_consecutive_pindirs(pio, sm, enc_pins.b, 1, false);

        pio_sm_config c = encoder_program_get_default_config(pio_program_offset[pio_idx]);
        sm_config_set_jmp_pin(&c, enc_pins.a);
        sm_config_set_in_pins(&c, enc_pins.b);

        sm_config_set_in_shift(&c, false, false, 1);
        sm_config_set_fifo_join(&c, PIO_FIFO_JOIN_RX);

        sm_config_set_clkdiv_int_frac(&c, freq_divider, 0);

        pio_sm_init(pio, sm, pio_program_offset[pio_idx], &c);

        hw_set_bits(&pio->inte1, PIO_IRQ1_INTE_SM0_RXNEMPTY_BITS << sm);
        if (claimed_sms[pio_idx] == 0)
        {
          // Configure the processor to run pio_handler() when PIO IRQ 0 is asserted
          if (pio_idx == 0)
          {
            irq_add_shared_handler(PIO0_IRQ_1, pio0_interrupt_handler, PICO_SHARED_IRQ_HANDLER_DEFAULT_ORDER_PRIORITY);
            irq_set_enabled(PIO0_IRQ_1, true);
          }
          else
          {
            irq_add_shared_handler(PIO1_IRQ_1, pio1_interrupt_handler, PICO_SHARED_IRQ_HANDLER_DEFAULT_ORDER_PRIORITY);
            irq_set_enabled(PIO1_IRQ_1, true);
          }
        }
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

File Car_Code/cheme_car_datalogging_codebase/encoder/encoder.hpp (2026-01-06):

#pragma once

#include "hardware/pio.h"
#include "pimoroni_common.hpp"

using namespace pimoroni;

namespace encoder
{
  static constexpr float MMME_CPR = 12.0f;
  static constexpr float ROTARY_CPR = 24.0f;

  class Encoder
  {
    //--------------------------------------------------
    // Constants
    //--------------------------------------------------
  public:
    static constexpr float DEFAULT_COUNTS_PER_REV = ROTARY_CPR;
    static const bool DEFAULT_COUNT_MICROSTEPS = false;
    static const uint16_t DEFAULT_FREQ_DIVIDER = 1;

  private:
    static const uint32_t STATE_A_MASK = 0x80000000;
    static const uint32_t STATE_B_MASK = 0x40000000;
    static const uint32_t STATE_A_LAST_MASK = 0x20000000;
    static const uint32_t STATE_B_LAST_MASK = 0x10000000;

    static const uint32_t STATES_MASK = STATE_A_MASK | STATE_B_MASK |
                                        STATE_A_LAST_MASK | STATE_B_LAST_MASK;

    static const uint32_t TIME_MASK = 0x0fffffff;

    //--------------------------------------------------
    // Enums
    //--------------------------------------------------
  private:
    enum StepDir
    {
      NO_DIR = 0,
      INCREASING = 1,
      DECREASING = -1,
    };

    enum MicroStep : uint8_t
    {
      MICROSTEP_0 = 0b00,
      MICROSTEP_1 = 0b10,
      MICROSTEP_2 = 0b11,
      MICROSTEP_3 = 0b01,
    };

    //--------------------------------------------------
    // Substructures
    //--------------------------------------------------
  public:
    class Capture
    {
      //--------------------------------------------------
      // Variables
      //--------------------------------------------------
    private:
      int32_t captured_count;
      int32_t captured_delta;
      float captured_frequency;
      float counts_per_rev;

      //--------------------------------------------------
      // Constructors
      //--------------------------------------------------
    public:
      Capture();
      Capture(int32_t count, int32_t delta, float frequency, float counts_per_rev);

      //--------------------------------------------------
      // Methods
      //--------------------------------------------------
    public:
      int32_t count() const;
      int32_t delta() const;
      float frequency() const;

      float revolutions() const;
      float degrees() const;
      float radians() const;

      float revolutions_delta() const;
      float degrees_delta() const;
      float radians_delta() const;

      float revolutions_per_second() const;
      float revolutions_per_minute() const;
      float degrees_per_second() const;
      float radians_per_second() const;
    };

    //--------------------------------------------------
    // Variables
    //--------------------------------------------------
  private:
    PIO pio;
    uint sm;
    pin_pair enc_pins;
    uint enc_common_pin;
    Direction enc_direction;
    float enc_counts_per_rev;

    const bool count_microsteps;
    const uint16_t freq_divider;
    const float clocks_per_time;

    //--------------------------------------------------

    volatile bool enc_state_a = false;
    volatile bool enc_state_b = false;
    volatile int32_t enc_count = 0;
    volatile int32_t enc_cumulative_time = 0;
    volatile int16_t enc_step = 0;
    volatile int16_t enc_turn = 0;
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

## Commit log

2026-01-06 initial commit of last year's work
    [Car_Circuitry.PrjPcb, Car_Circuitry.SchDoc, Car_Circuitry.step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]
2026-01-06 updated to reflect nationals design
    [Car_Circuitry.PrjPcb, Car_Circuitry.SchDoc, Steering_Daughterboard.PcbDoc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]
2026-01-06 added holes
    [Car_Circuitry.PcbDoc, Car_Circuitry.step, Steering_Daughterboard.step]
2026-01-22 Updated schematic and PCB with sound playing components
    [Car_Circuitry.SchDoc]
2026-01-23 Completed PCB With Sound Circuit
    Fixed errors in old PCB
2026-01-25 updated step model, minor changes to speaker amp circuit to improve noise filtering.
    [Car_Circuitry.PcbDoc, Car_Circuitry.SchDoc, Car_Circuitry.step]
2026-01-26 Resolve stash conflict: apply PT schematic/PCB changes
    [Car_Circuitry.PcbDoc, Car_Circuitry.SchDoc]
2026-01-28 Final board updates before fabrication, more & smaller vias, re-worked minor placement of parts, finalized graphics.
    [Car_Circuitry.PrjPcb, Car_Circuitry.SchDoc, Car_Circuitry.step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]
2026-02-03 update assembly drawing
2026-02-08 Wrote code to setup and initialize I2C sensor, plus a helper function to read from a register eventually
2026-02-24 Added DC Motor Control and Added Door Opening and Closing Sequence Functions
2026-03-06 Updated sample averaging in datalogging codebase
2026-03-06 Added I2C sensor integration and helper functions for voltage/current monitoring in competition code
2026-03-06 Updated led
2026-03-09 I incorporated the ssr motor drive and brake by redefining the pins to the updated version and created new functions for driving and braking called drive_ssr and brake_ssr. Updated the steering to do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
2026-03-11 fixed encoder datalogging since that was overwritten in previous merge.
    [cheme_car_datalogging_codebase.ino]
2026-03-11 formatting & missing bracket & arguments.
    [cheme_car_competition_codebase.ino, cheme_car_datalogging_codebase.ino]
2026-03-11 servo dumping pins were swapped, fixed.
    [Car_Circuitry.SchDoc, Car_Circuitry_BOM.xlsx]
2026-03-16 Fixed changes and cleaned up code
    removed temp comments and made sure code was consistent across both files
    [cheme_car_competition_codebase.ino, cheme_car_datalogging_codebase.ino]
2026-03-18 reverted PCB stuff to master branch copies
    [Car_Circuitry.PrjPcb, Car_Circuitry.SchDoc, Car_Circuitry.step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]
2026-03-18 works but no voltage & encoder issues
    [cheme_car_competition_codebase.ino, cheme_car_datalogging_codebase.ino]
2026-03-18 voltage working, encoder needs testing.
2026-03-19 updated schematic (wrong pins again), changed braking stir speed.
    [Car_Circuitry.SchDoc]
2026-03-20 Update cheme_car_competition_codebase.ino
    Slightly altered audio playing logic, added function to turn off speaker when not in use. Added lines to turn off stirring motor when car is done its run.
2026-03-21 brake sooner
2026-03-24 update PID
2026-04-07 mostly working, check buffer overflow & flux capacitor issue.
    [cheme_car_competition_codebase.ino, cheme_car_datalogging_codebase.ino]
2026-04-08 Fixed speaker, added final SFX
    [cheme_car_competition_codebase.ino, cheme_car_datalogging_codebase.ino]
2026-04-17 cut time circuit sound & starting delays
